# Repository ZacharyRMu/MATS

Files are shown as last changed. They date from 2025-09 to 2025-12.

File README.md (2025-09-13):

# Mobile Antenna Tracking System (MATS)

<p align="center">
  <picture>
    <source media="(prefers-color-scheme: dark)" srcset="docs/images/MATS_Logo_White.png">
    <source media="(prefers-color-scheme: light)" srcset="docs/images/MATS_Logo_Black.png">
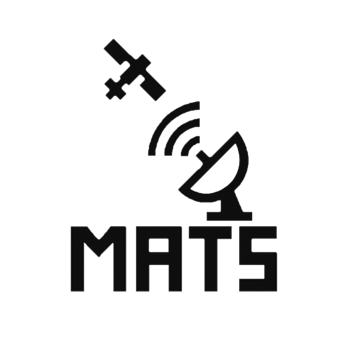
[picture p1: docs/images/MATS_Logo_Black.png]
MATS Logo
    
  </picture>
</p>

## Overview
MATS (Mobile Antenna Tracking System) is a portable ground station platform designed to automatically track and recieve data from Low Earth Orbit (LEO) weather satellites. The system integrates: 
- Reciever Subsystem - Raspberry Pi 5 with SDR Hardware, SatDump, SDR++, and GPS timing. 
- Rotator Subsystem - Motorized antenna rotator with gearing and fixture assembly for precise azimuth/elevation pointing. 
- User Interface (UI) - Touchscreen controls, pass scheduling via Gpredict, and system health/status indicators. 
- Power Subsystem - Regulated DC rails providing reliable power to the Pi, motors, and peripherals. 

## Features 
- Automated Satellite pass prediction and antenna tracking.
- Real-time SDR signal aquisition and decoding via SatDump.
- Portable Architecture for field deployments 
- Open, Modular Design for extensibility. 
## Installation and Setup 
1. Receiver Subsystem 
    - Flash Raspberry Pi OS on a Pi 5. 
    - Run the provided install script to set up SatDump, SDR++, Gpredict, and required libraries. 
    ```bash 
    cd Receiver
    ./batch_installer.sh
2. Rotator Subsystem
    - Assemble Mechanical fixture (CAD models in [placeholder]). 
    - Flash motor control firmware to microcontroller. 
3. UI Subsystem 
    - Connect Pi Touchscreen 
    - Run UI code to access controls and system status. 

## Usage
- Use **Gpredict** to select a satellite pass. 
- The **Rotator** will align the antenna in real time. 
- SatDump automatically records and decodes the downlink. 
- Results are stored in `/Receiver/Data/` and can be reviewed via the UI.

## License
This project is licensed under the GNU General Public License V3.0 (GPL-3.0). You may redistribute and modify it under the terms of the GPL as published by the Free Software Foundation. 

## Acknowledgements & External Software 
MATS leverages several excelled open-source projects: 
- [SatDump](https://github.com/SatDump/SatDump_) - Satellite signal demodulation and decoding. (Licensed under GPL-3.0)
- [SDR++](https://github.com/AlexandreRouma/SDRPlusPlus) - Software-defined radio receiver. (Licensed under GPL-3.0)
- [Gpredict](https://github.com/csete/gpredict) - Real-time satellite tracking and orbit protection. (Licensed under GPL-2.0)
- [VOLK](https://github.com/gnuradio/volk_) - Vector-optimized library of Kernels used by GNU Radio. (Licensed under GPL-3.0)

We extend sincere thanks to these communities for providing the tools that make this project possible.

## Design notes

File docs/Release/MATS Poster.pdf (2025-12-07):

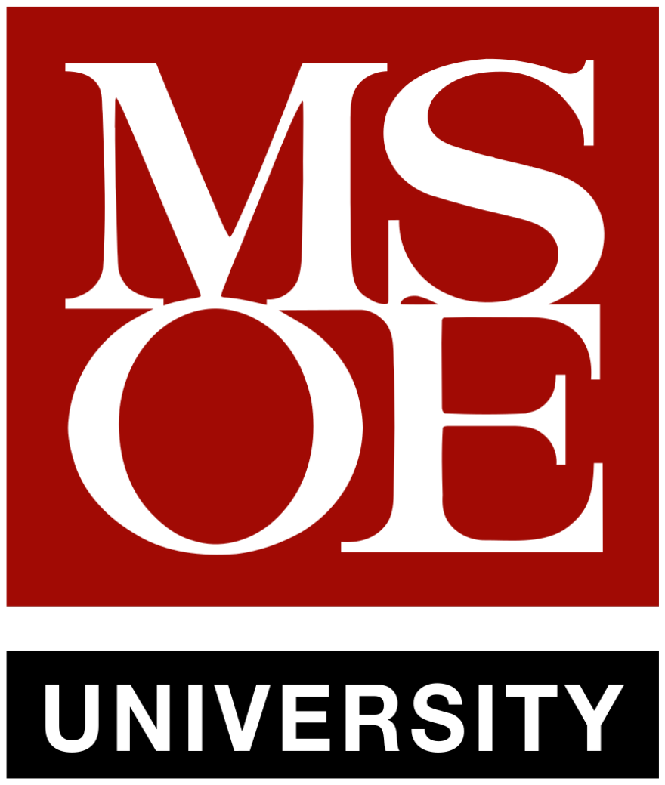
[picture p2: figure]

# MATS - Mobile Antenna Tracking System

# A Smart Portable Antenna Rotator and Satellite Receiver for Weather Imagery

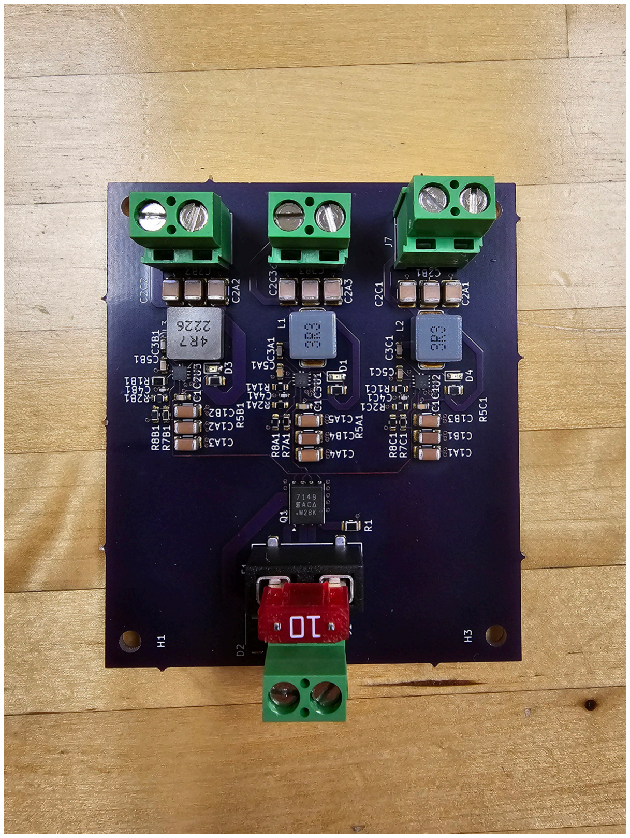
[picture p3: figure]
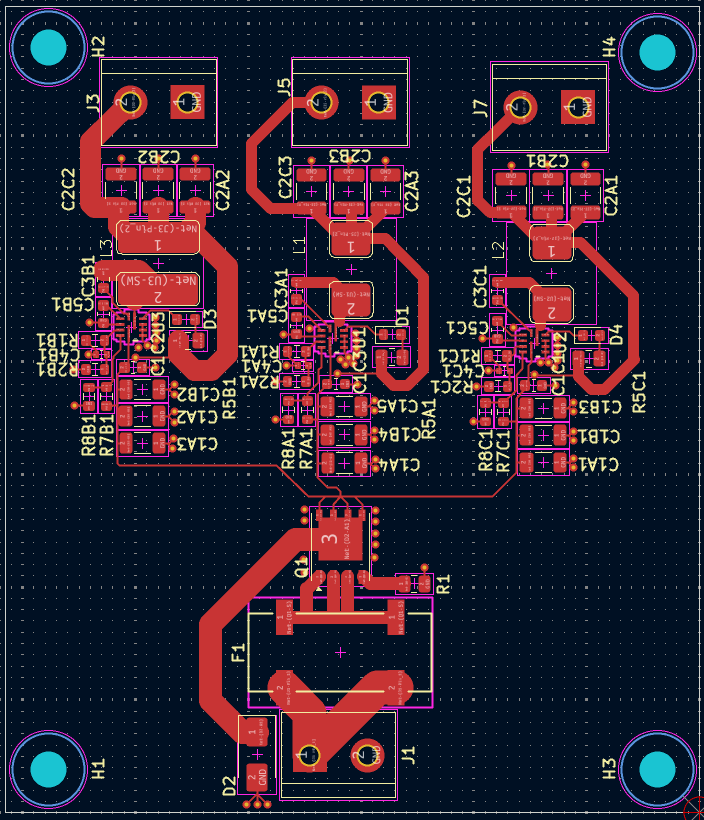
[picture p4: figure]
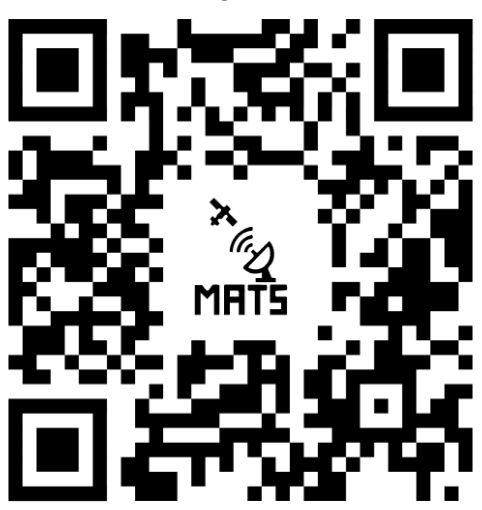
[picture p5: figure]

# Our Team

Zachary Murray, Dylan Vilcek, Ma Minghao

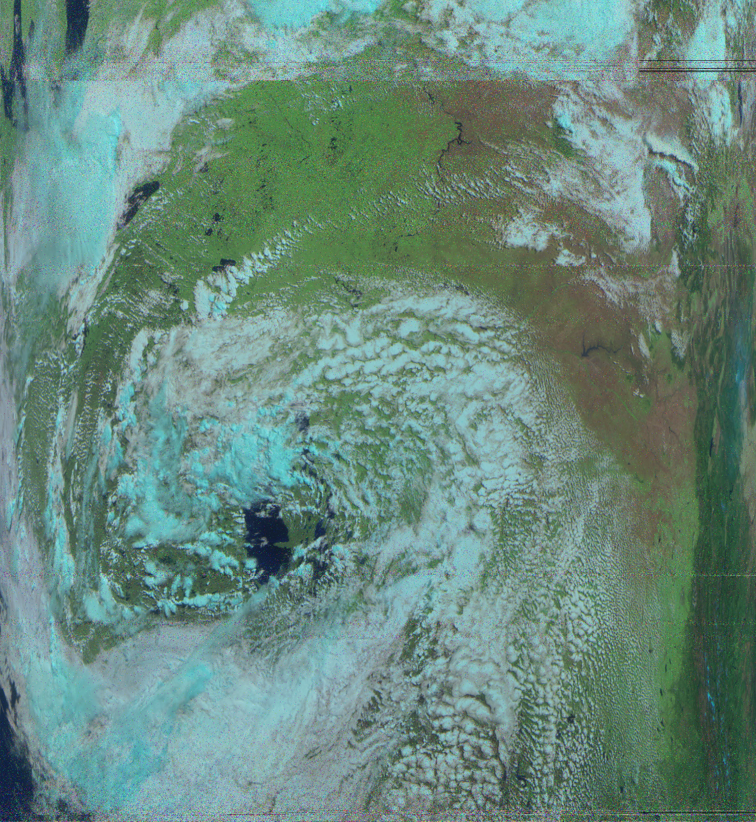
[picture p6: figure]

# Learn More

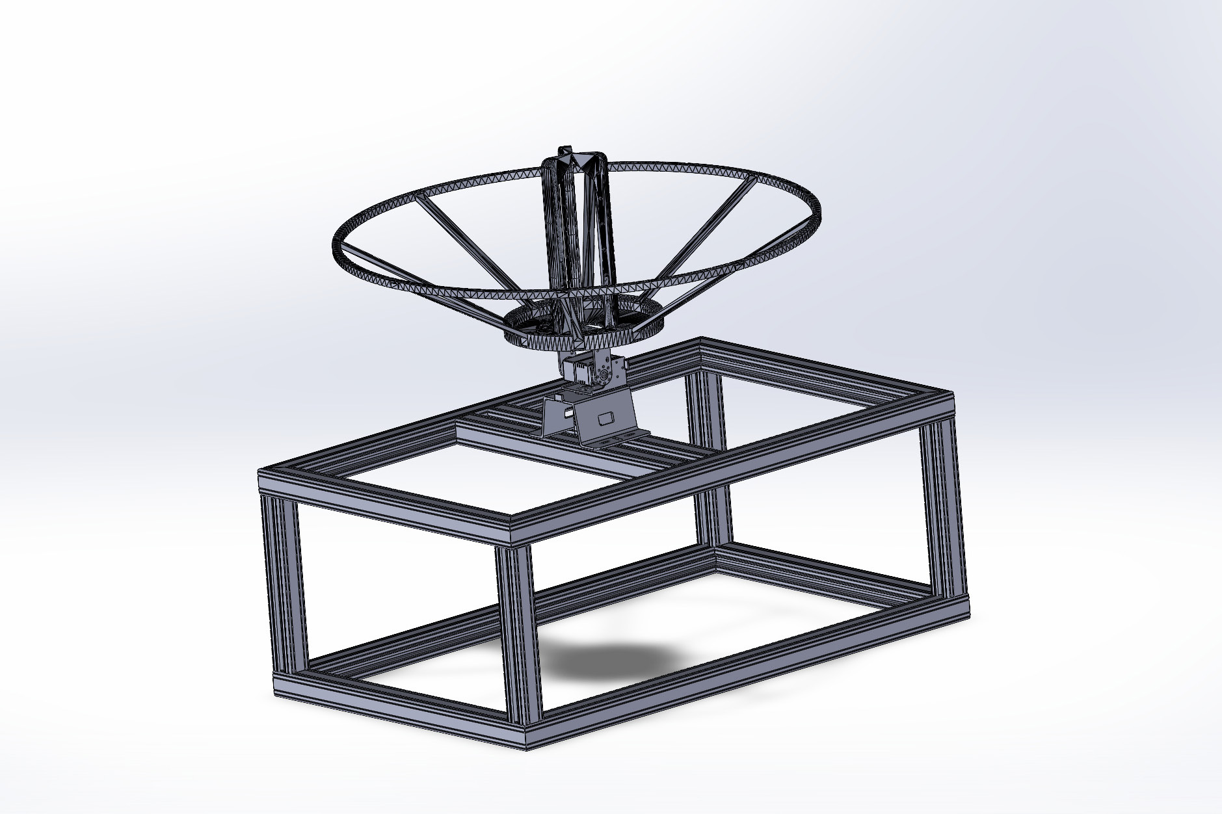
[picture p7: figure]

# System Block Diagram

The team would like to thank both Field Theory Consulting and MSOE alumnus Mr. Bob Radke for generous donations of materials for this project. Special thanks to our advisor, Dr. Kelnhofer for guidance and support.

# Acknowledgments

- Low cost, portable, and deployable on aircraft, ships, or field vehicles
- Operates from common on-board power (12-24VDC)
- Compact and Lightweight (<25 lbs, 22x14x9 in)
- Modular design supporting various types of antennas and receivers
- Reliably acquires and decodes L-band and other weather satellite signals
- Uses readily available hardware and open-source software

# Problem Statement

Existing satellite tracking systems are often expensive, proprietary, and difficult to use. MATS provides an open, modular platform for precise, automated multi-axis tracking and reception, designed for off-grid pilots, emergency crews, researchers, and educators.

# System Goals

# Technical Targets

- Achieve automated azimuth/elevation tracking within 1%
- Integrate GPredict tracking data over I²C
- Provide modular power rails (7.5 V, 5 V, 3.3 V)
- Support open-source SDR decoding (SatDump)

Power System PCB Layout and Assembly

Example Satellite Weather Imagery Captured

Pictured: Mechanical System

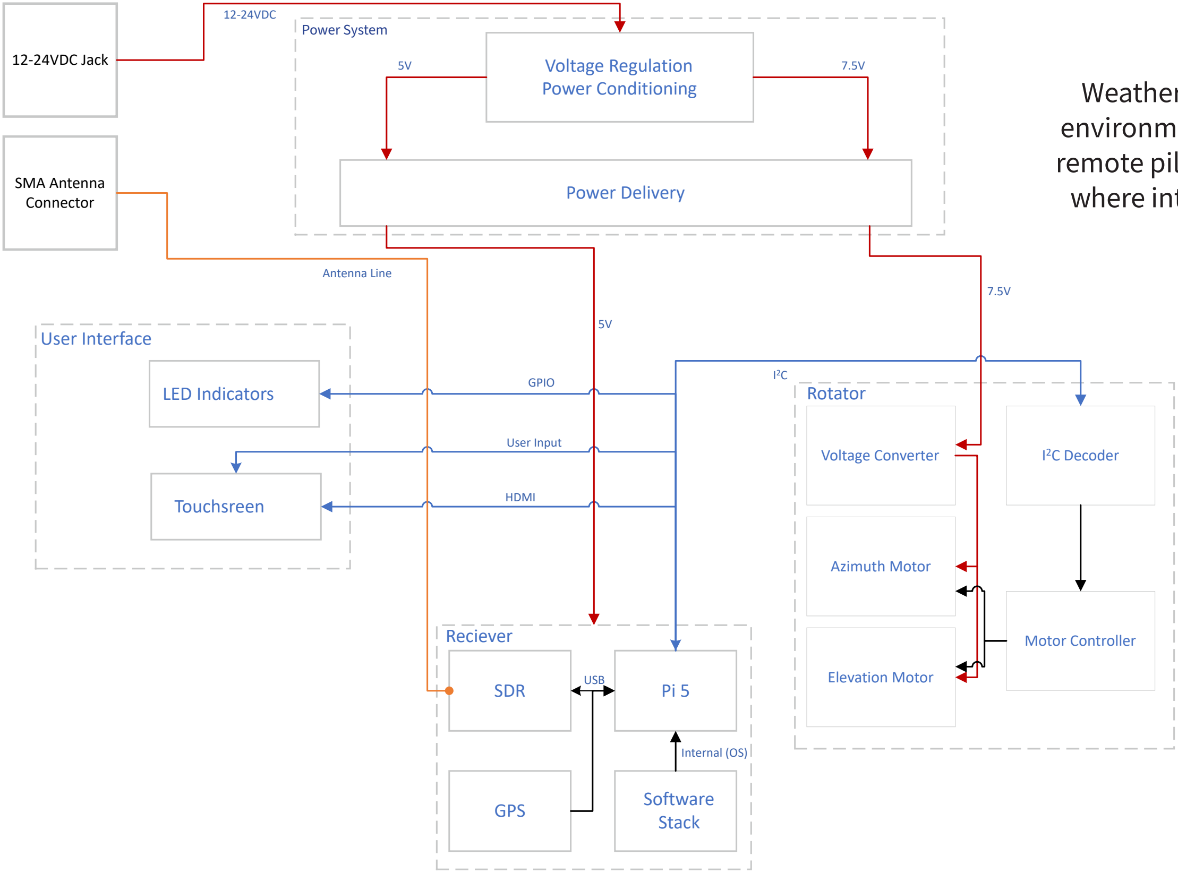
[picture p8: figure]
User Interface; Voltage Converter; Azimuth Motor; Elevation Motor; 2C Decoder; Reciever; Motor Controller; SDR; Software Stack; GPS; USB; Internal (OS); LED Indicators; Rotator; Touchsreen; HDMI; GPIO; User Input; Voltage Regulation Power Conditioning; Power Delivery; 12-24VDC Jack; SMA Antenna Connector; Antenna Line; 12-24VDC; Power System

Weather imagery provides critical near real time environmental data for emergency response crews, remote pilots, and research crews stationed in areas where internet may not be available or expensive.

## Find the Project on GitHub

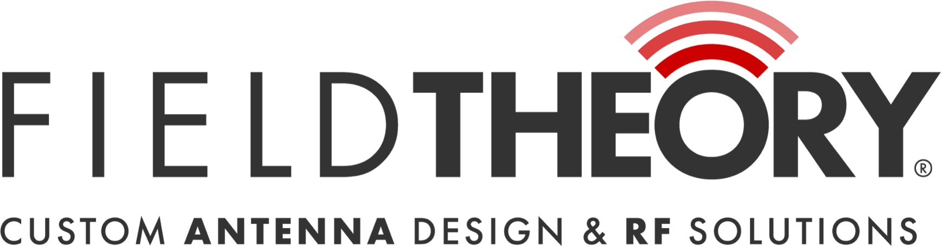
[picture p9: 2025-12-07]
docs/images/fieldtheory.jpg

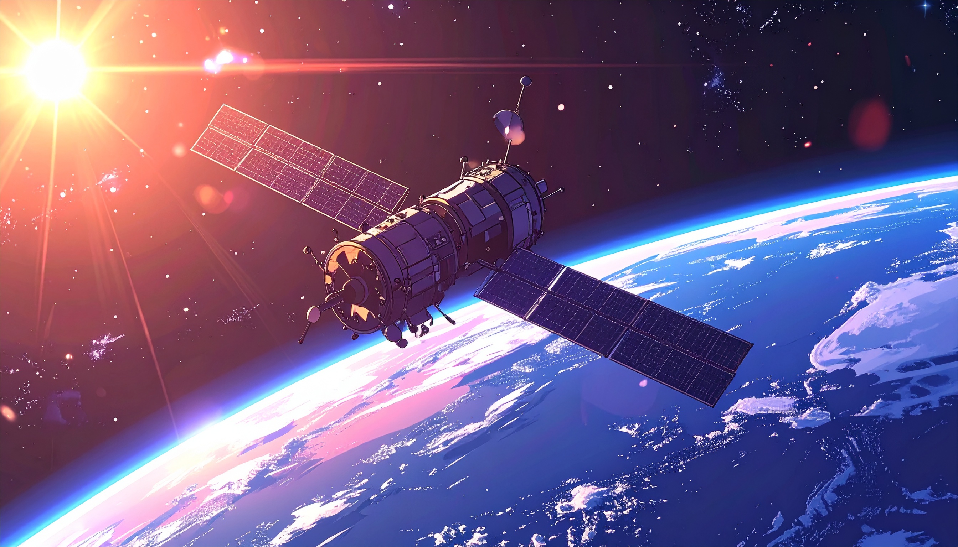
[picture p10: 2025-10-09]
docs/images/MATS_Background.jpg

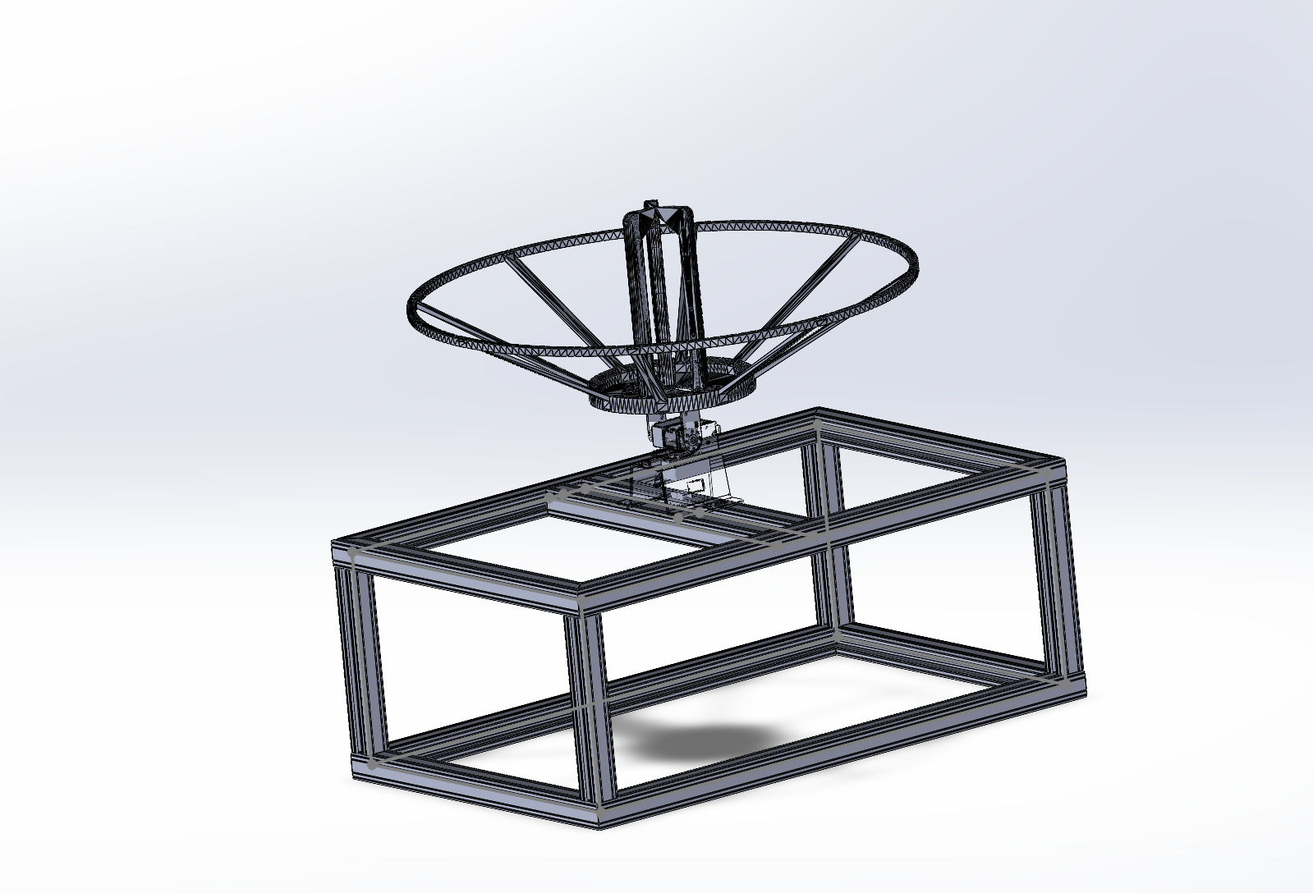
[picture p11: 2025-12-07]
docs/images/Screenshot 2025-12-01 123529.png

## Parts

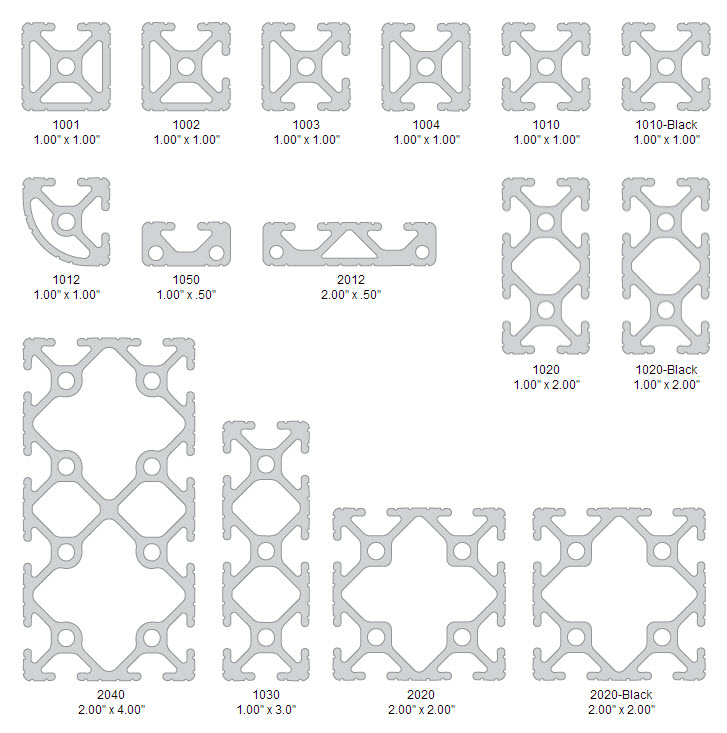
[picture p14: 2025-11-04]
Mechanicals/parts/weldment/Renderings/10_series_image_list.jpg

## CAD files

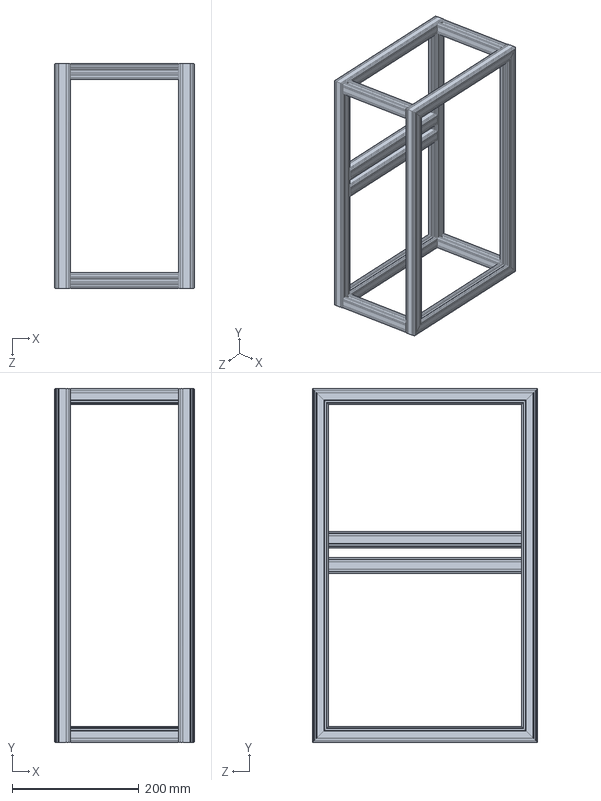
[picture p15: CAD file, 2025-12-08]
Mechanicals/Case/weldment.SLDPRT
221.5 x 558.8 x 355.6 mm

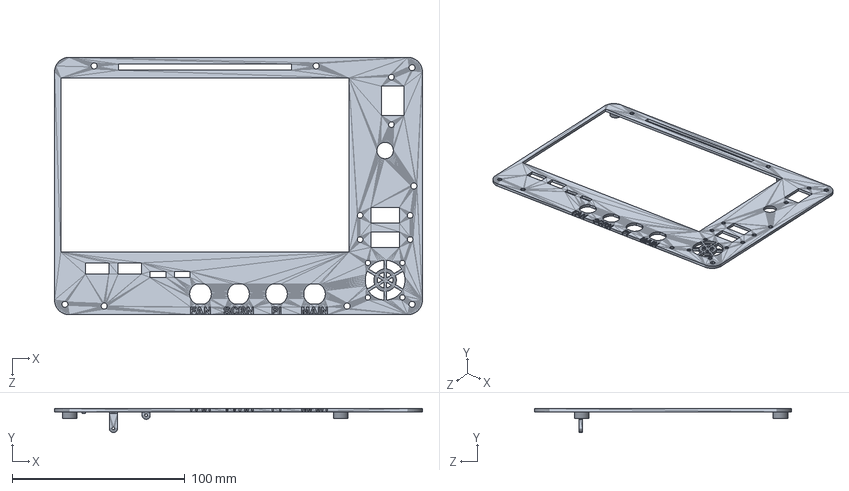
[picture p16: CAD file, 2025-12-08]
Mechanicals/parts/Screenpanel.SLDPRT
213.0 x 13.9 x 149.0 mm

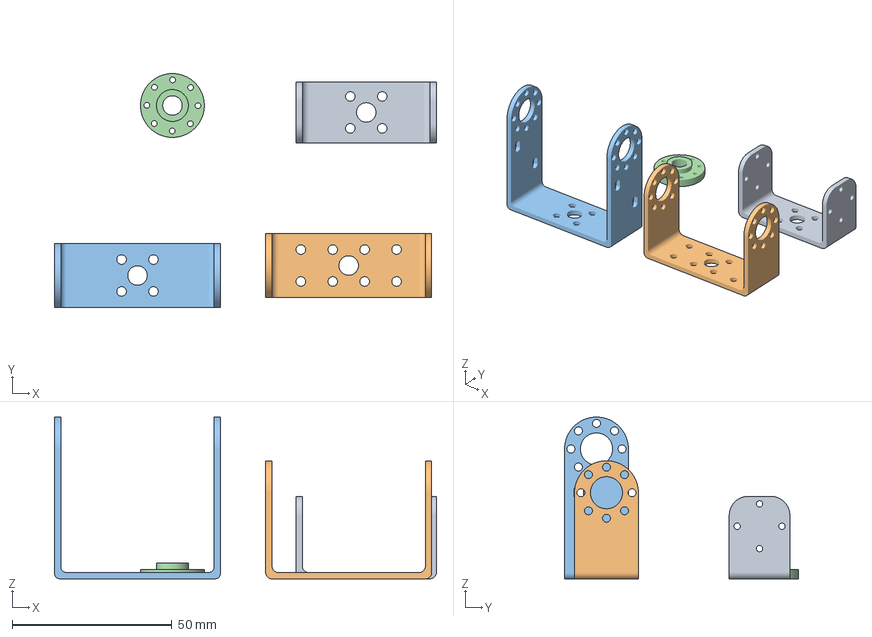
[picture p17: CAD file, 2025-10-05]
Mechanicals/Servo Motor Mount Print.3mf
119.6 x 73.2 x 50.7 mm
华馨京 25-50kg舵机系列U型舵盘支架（标准）-3D.STEP
华馨京 25-50kg舵机系列U型舵盘支架（37mm）-3D.STEP
华馨京 25-50kg舵机系列U型舵盘支架（50.7mm）-3D.STEP
华馨京 25-50kg舵机系列副舵盘-3D.STEP

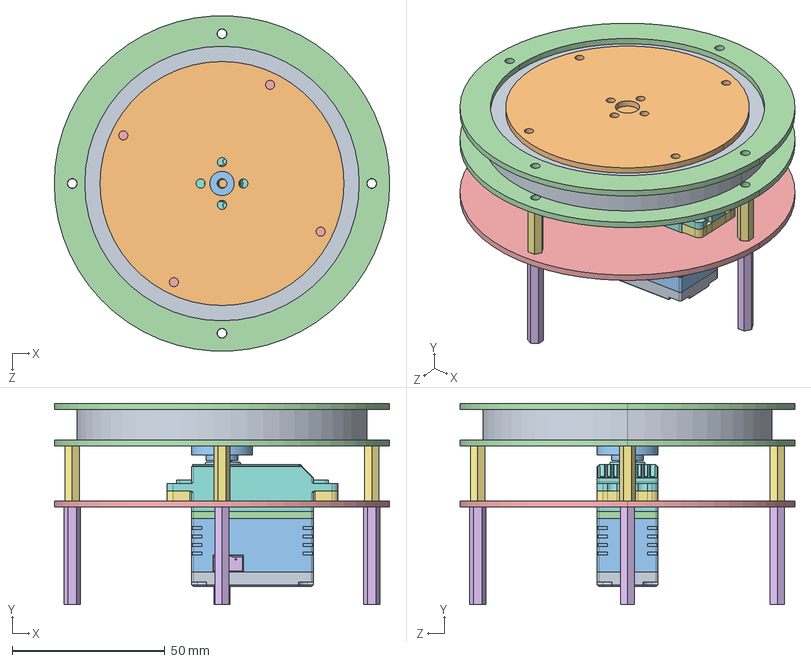
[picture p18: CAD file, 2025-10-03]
Mechanicals/华馨京科技 舵机云台系列图纸/华馨京科技 PD1-H-1 一维圆盘云台图纸/华馨京 圆盘云台-3D.STEP
110.0 x 66.0 x 109.8 mm
ZHOUCHENG^2自由度云台(2)_2自由度云台
ZHOUCHENGNEIBAN^2自由度云台(2)_2自由度云台 x 2
DUOPAN^2自由度云台(2)_2自由度云台
ZHOUCHENGWAIBAN^2自由度云台(2)_2自由度云台 x 2
ZHOUCHENGXIABAN^2自由度云台(2)_2自由度云台
TONGZHU32^2自由度云台(2)_2自由度云台 x 4
TONGZHU18^2自由度云台(2)_2自由度云台
TONGZHU^2自由度云台(2)_2自由度云台 x 4
____________.step.STEP
____________.step-0.STEP
______.step.STEP
____-____.STEP
________.STEP
3pin____.step.STEP x 2
单轴舵机垫片.stp x 2

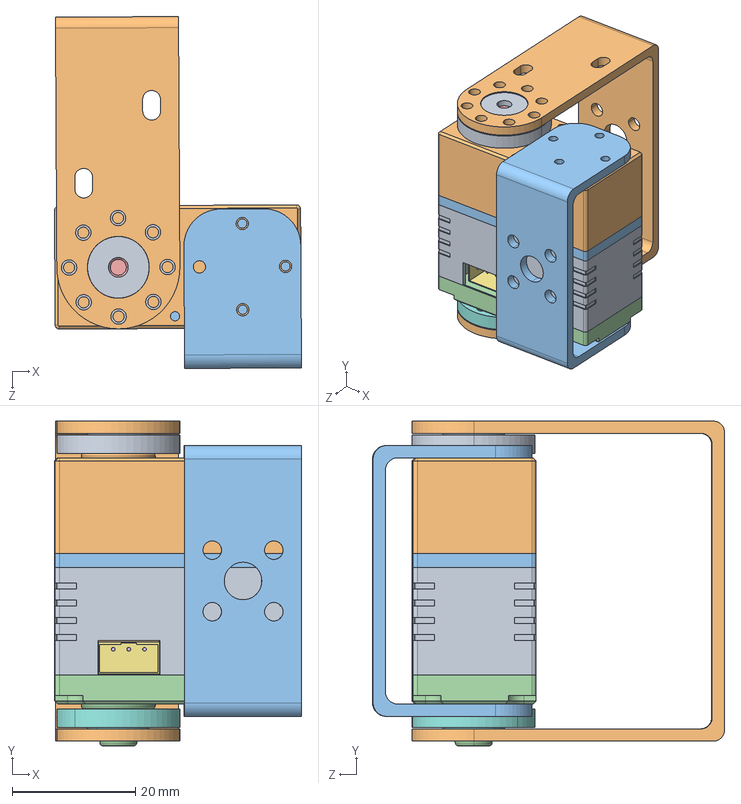
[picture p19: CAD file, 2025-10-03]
Mechanicals/华馨京科技 舵机云台系列图纸/华馨京科技 PD1-R-1 简易云台图纸/华馨京 简易云台-3D.STEP
40.1 x 52.8 x 57.2 mm
____-____.STEP
____________.STEP
________.STEP
____________-0.STEP
______.step.STEP
3pin____.step.STEP x 2
嗆攫ㄗ萵ㄘ
嗆攫ㄗ翋ㄘ
华馨京 25-50kg舵机系列长U1支架-3D
华馨京 25-50kg舵机系列小U支架-3D

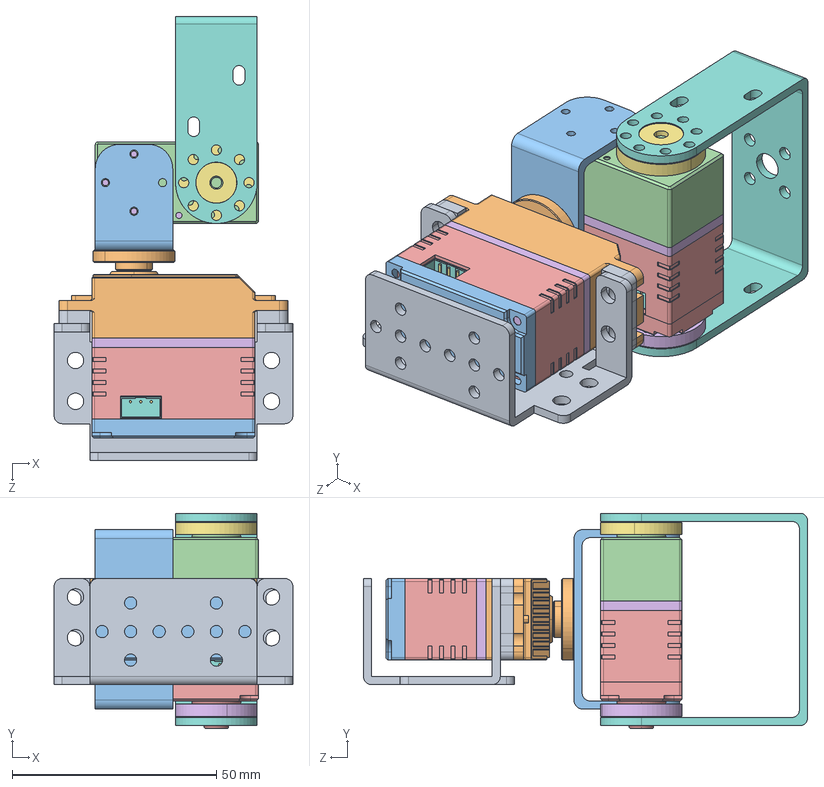
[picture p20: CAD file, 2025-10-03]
Mechanicals/华馨京科技 舵机云台系列图纸/华馨京科技 PD2-RH-1 二维多功能云台图纸/华馨京 多功能云台-3D.STEP
58.5 x 52.8 x 108.7 mm
多功能支架
____________.step.STEP
____________.step-0.STEP
______.step.STEP x 2
____-____.STEP x 2
________.STEP x 2
3pin____.step.STEP x 4
单轴舵机垫片.stp x 2
华馨京 25-50kg舵机系列主舵盘（四孔）-3D
华馨京 25-50kg舵机系列小U支架-3D
____________.STEP
____________-0.STEP
嗆攫ㄗ萵ㄘ
嗆攫ㄗ翋ㄘ
华馨京 25-50kg舵机系列长U1支架-3D

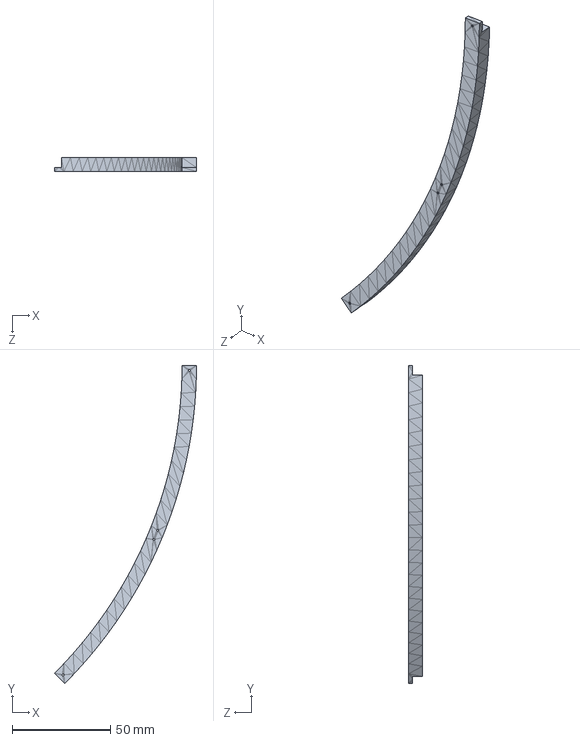
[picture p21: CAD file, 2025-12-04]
Mechanicals/parts/Upper_ring_x8.SLDPRT
72.4 x 162.1 x 7.00 mm

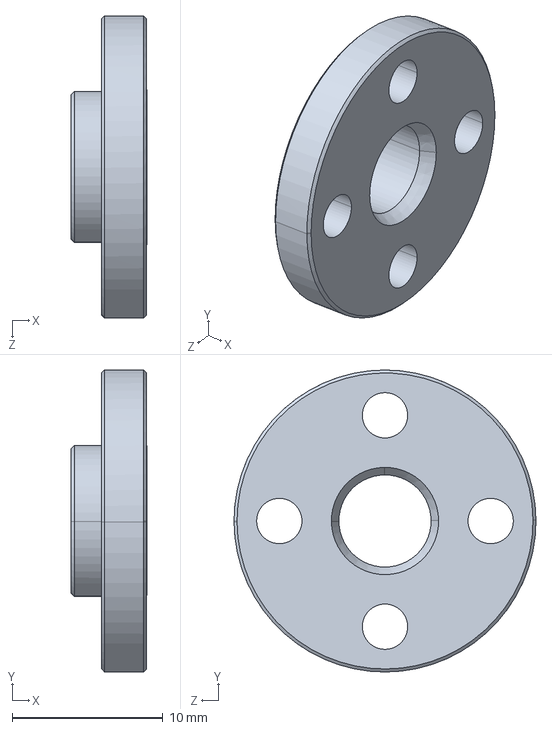
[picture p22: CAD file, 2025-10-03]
Mechanicals/华馨京 25-50kg舵机系列副舵盘（四孔）-3D.STEP
5.00 x 20.0 x 20.0 mm

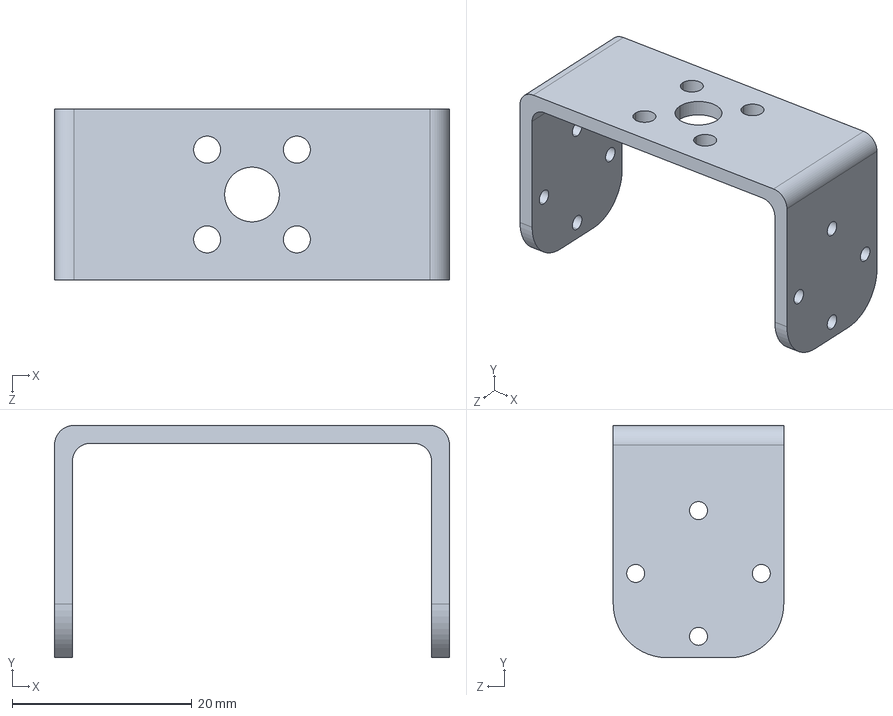
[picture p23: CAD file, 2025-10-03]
Mechanicals/华馨京 25-50kg舵机系列配件/华馨京 25-50kg舵机系列U型舵盘支架（标准）-3D.STEP
44.0 x 25.9 x 19.0 mm

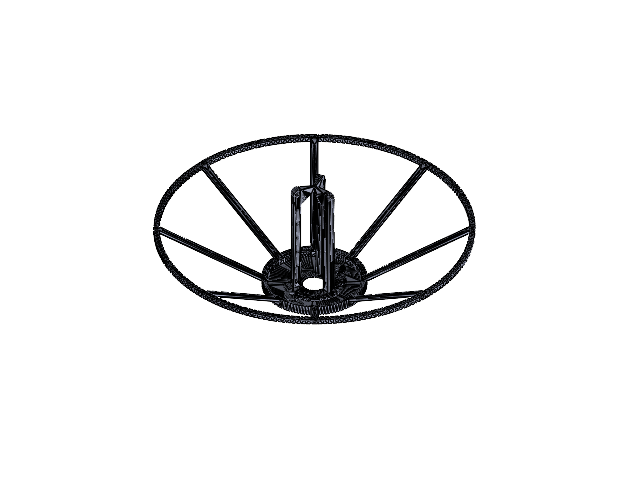
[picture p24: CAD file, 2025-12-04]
Mechanicals/parts/antenna.SLDASM
Base
Upper_ring_support_x8 x 8
Upper_ring_x8 x 8
helix_support_6.5T_1.7_Ghz

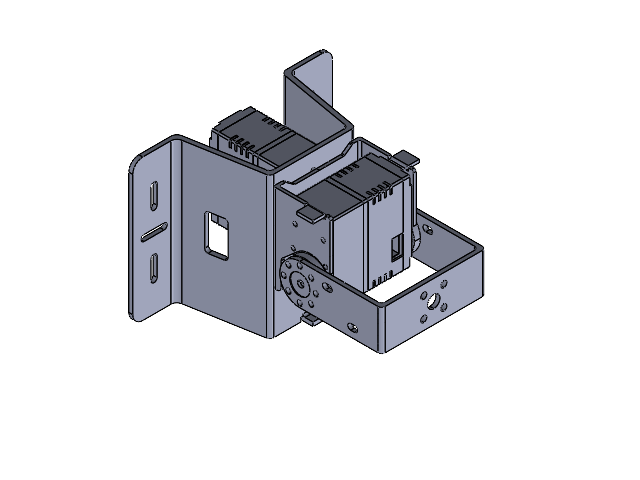
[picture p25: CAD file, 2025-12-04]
Mechanicals/parts/华馨京 OpenMV舵机云台-3D.SLDASM
____-____.STEP.STEP x 2
____________.STEP.STEP x 2
________.STEP.STEP x 2
____________-0.STEP.STEP x 2
______.step.STEP.STEP x 2
3pin____.step.STEP.STEP x 4
______________,______.STEP
__________.STEP
__________-0.STEP x 2
________________.step.STEP
__U________.STEP

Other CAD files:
Mechanicals/parts/weldment/001_t_slot_ty3_asm_27.sldasm
Mechanicals/parts/grainger-815GF4.sldasm
Mechanicals/parts/weldment/815gf5_2.sldprt
Mechanicals/华馨京 25-50kg舵机系列配件/华馨京 25-50kg舵机系列副舵盘尺寸图.dwg
Mechanicals/华馨京科技 OpenMV舵机云台图纸/华馨京 OpenMV舵机云台外观尺寸图.dwg
Mechanicals/华馨京科技 舵机云台系列图纸/华馨京科技 OpenMV舵机云台图纸/华馨京 OpenMV舵机云台外观尺寸图.dwg
Mechanicals/华馨京科技 舵机云台系列图纸/华馨京科技 PD2-RH-2 二维大支架云台图纸/华馨京 大支架云台外观尺寸图.dwg
Mechanicals/Case/Frame.SLDDRW
Mechanicals/parts/Base.SLDPRT
Mechanicals/parts/Base.stl
Mechanicals/parts/Dual-axis servo.SLDPRT
Mechanicals/parts/Dual-axis servo.STEP
Mechanicals/parts/Screenpanel.stl
Mechanicals/parts/Single axis servo.STEP
Mechanicals/parts/Upper_ring_support_x8.SLDPRT
Mechanicals/parts/Upper_ring_support_x8.stl
Mechanicals/parts/Upper_ring_x8.stl
Mechanicals/parts/antenna_mount.SLDPRT
Mechanicals/parts/helix_support_6.5T_1.7_Ghz.stl
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

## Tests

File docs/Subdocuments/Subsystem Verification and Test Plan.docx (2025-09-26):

MATS Subsystem Test Plans

Mobile Antenna Tracking System (MATS)

9/26/2025

Zachary Murray, Dylan Vilcek, Ma Minghao


This document outlines the subsystem verification and test plan for the MATS. This document will outline the objectives of testing each subsystem, equipment and software required, as well as the procedures to verify the proper operation of the individual subsystems for successful integration into the overall system.

Revision | Date | Author | Description
0.1 | 9/26/2025 | MATS Team | Initial draft created

# Receiver

## Subsystem Overview

The receiver is responsible for being the central processor for the MATS. Its duties include being able to track a satellite given the TLE’s in Gpredict, receiving signals from the tracked satellites and decode the signals using SatDump. The receiver is equipped with an RTL-SDR for signal reception and utilizes a Raspberry Pi 5 running Raspian OS for its wide software support and community. Additionally, the Receiver subsystem will be equipped with GPS such that SatDump can accurately decode the received signals with map overlays and timestamps. To support the tracking of the satellite, the Receiver utilizes its GPS coordinates and the TLE data given by Gpredict and sends position data to the Rotator.

## Subsystem Requirements and Specifications

To enable the Receiver to function accurately and be integrated into the MATS successfully, the Receiver has the following signal characteristics and requirements.

Table 1: Receiver Subsystem Requirements

Receiver Subsystem
Power Requirement | 5VDC 5A
I/O Characteristics | USB2-A Interface HDMI I2C
Receiving Equipment | 50Ω Antenna line External SMA Antenna Connector
Software | Raspbian OS SatDump Gpredict RTL-SDR drivers/software

## Objectives

The objectives for testing the receiver include verifying that the receiver has the correct drivers and software stack, being able to receive satellite communication downlinks, and decode these downlinks into meaningful data. Subsystem components that will be tested include:

- Installation of the correct RTL-SDR Drivers
- I2C enabled
- Correct software stack installed
  - SatDump
  - GPredict
  - GPS Driver
  - SDR++
- Reception of common satellites
- Satellite transmission decodes

These objectives ensure that the receiver can correctly send commands via I2C, receive and decode Satellite transmissions. Early testing to verify the I2C bus sends the correct 32 bits will also be executed, ensuring smooth integration with the rotator.

## Required Equipment

The required equipment to test the Receiver can be found below. Additionally, the testing scripts and programs can be found at the project’s GitHub[^1]. Required hardware testing is as follows:

- Receiver hardware
- Analog Discovery 2
- V-Dipole if testing VHF or equivalent L-band antenna if testing using L-band (can substitute for other antennas as region requires.)
- Multimeter

Optional equipment is listed below for use with certain testing scripts and hardware but not necessarily required:

- Laptop with serial port
- NanoVNA
- LNA/LNB for satellite reception (Satellite Dependent)

## Testing Procedure

### Correct Drivers Installed

Installation of the correct RTL-SDR drivers is crucial. The installer script should fetch the latest version, build, and install the correct driver. However, sometimes Udev rules can become a problem and not allow the correct RTL-SDR driver to initialize; it’s important that it is checked to verify that the correct driver is installed, and the generic driver be disabled. To ensure that the correct drivers are installed, Table 2 outlines the procedure to be followed.

Table 2: Correct RTL-SDR Driver Install Test Procedure

Test | Expected Result | Observed Result
Check that DVB and rtl12832 drivers are not loaded using lsmod | Drivers not loaded
Plug in RTL-SDR V4 into Receiver | N/A | N/A
Run lsusb to confirm the device is detected | RTL-SDR found
Run rtl_test -t or rtl_test -p to verify the driver claims the device | No "usb_open error" message

### I2C Interface Enablement

Verify that the Raspberry Pi’s I2C interface is enabled by the installer script and accessible by user-space applications. Table 3 outlines this procedure.

Table 3: I2C Interface Testing

Test | Expected Result | Observed Result
Inspect /boot/firmware/config.txt
Confirm dtparam=i2c_arm=on is present and not commented out | Line not commented out
Verify the invoking user has been added to the i2c group
run the following: groups $USER | grep i2c | User Added
Verify the kernel driver is loaded. Run: lsmod | grep i2c_bcm | Driver loaded
With the system booted, execute: sudo i2cdetect -y 1 | A grid of addresses is displayed
Use the Analog Discovery 2 to verify I2C traffic using the provided i2c_ad2_test.py script. | I2C present on AD2

### Installed Software Stack

The receiver must have the correct software stack for correct operation with the other subsystems. This test section ensures that the correct software, such as GPS drivers, SatDump, Gpredict, and SDR++ are installed on the system. Table 4 shows the procedure. A test script has been provided in the github repository for automated testing.

Table 4: Receiver Software Stack Test Procedure

Test | Expected Result | Observed Result
Run automated verification script | Script executes and prints results for each component.
Check GPS drivers | Output shows: [+] Checking gpsd... PASS
Check SatDump installation | Output shows: [+] Checking SatDump... PASS
Check Gpredict installation | Output shows: [+] Checking Gpredict... PASS
Check SDR++ installation | Output shows: [+] Checking SDR++... PASS
Review summary | Script ends with === Verification complete === and no FAIL messages.

### Satellite Reception

Successful satellite reception is required for the MATS to perform it’s core functionality. Shown below in Table 5, the testing procedure verifies that that SatDump can record a satellite transmission.

Table 5: Satellite Reception Test

Test | Expected Result | Observed Result
Connect RTL-SDR Blog V4 dongle to Pi USB 3.0 port and attach VHF antenna (QFH, V-dipole, turnstile, etc.) tuned for ~137 MHz. | Hardware connected firmly, antenna outdoors or with clear sky view.
Use Gpredict to check upcoming Meteor-M2-4 pass (137.9 MHz). Record start time, max elevation, and pass duration. | Pass info visible, frequency: 137.900 MHz.
Launch SDR++ and configure RTL-SDR input. Set center frequency to 137.9 MHz and sample rate to ~2.048 MSPS. | Device initializes without error, spectrum visible.
Observe waterfall during predicted pass. | Wideband (~140 kHz) signal appears centered at 137.9 MHz, rising above noise floor as pass begins.
(Optional) Verify via SatDump spectrum mode without decoding. | Console/log shows device streaming, RF power increases near 137.9 MHz during pass.
Monitor until end of pass. | Signal fades as satellite sets. No USB or driver errors reported.

### Satellite Transmission Decoding

Testing of the receiver’s decoding stack ensures that satellite transmissions are accurately reconstructed with the correct GPS coordinates and map overlays. Table 6 below outlines the testing procedure.

Table 6: Satellite Transmission Decode Test

Test | Expected Result | Observed Result
Connect RTL-SDR Blog V4 dongle to Pi USB 3.0 port and antenna suitable for target satellite (e.g., QFH for VHF). | Hardware connected firmly, antenna with clear sky view. | Hardware connected firmly, antenna with clear sky view.
Use Gpredict to schedule and monitor an upcoming pass of a decodable satellite (e.g., NOAA APT at 137.1–137.9 MHz or Meteor-M2-4 at 137.9 MHz). | Pass data visible with start time, elevation, and duration.
Launch SatDump in live mode with correct frequency and sample rate. | SatDump initializes without error, SDR engaged.
Observe console/log during pass. | Frames are received and decoded; progress messages visible.
At end of pass, review generated products (e.g., map overlays, imagery, data files). | Output files (e.g., PNG, HDF5) are generated in SatDump output directory with valid content.

## Subsystem Test Results

After execution of all test sections (drivers, I2C, software stack, reception, and decoding), results should be consolidated in the following table.

Test Section | Pass/Fail | Notes
RTL-SDR Driver Install
I²C Interface Enablement
Software Stack Verification
Satellite Reception (M2-4, 137.9 MHz)
Satellite Transmission Decoding

# User Interface

## Subsystem Overview

The User Interface subsystem provides the primary operator touchpoint within the MATS. It delivers feedback through a 7” touchscreen, communicates system status via LED indicators, and provides removable media access through USB and SD ports. The UI runs a lightweight Raspberry Pi OS desktop, auto-launching SatDump at startup. Status LED’s are driven using a Python daemon that subscribes to SatDump telemetry, providing live feedback for RF lock, recording, and power state.

## Subsystem Requirements and Specifications

Table 7: User Interface Subsystem Specifications

Category | Requirement
Display | 7 Inch capacitive touchscreen with Linux driver support.
Inputs/outputs | ≥1 USB-A user port, SD/microSD card reader, power switch, RF & Power status LEDs.
Environmental | Operating 0ºC-50ºC, front panel IP-54 splash resistance
Electrical | Single 5V DC rail, ≤ 2A steady-state draw
Software | I2C touch controller, GPIO LEDs
Mechanical | Front-panel mounting to aluminum chassis, maximum depth behind panel ≤45 mm

## Objectives

The testing objectives for the User Interface are:

- Verify touchscreen responsiveness and accuracy
- Confirm automatic startup and SatDump launch.
- Validate USB and SD card hot-plug enumeration
- Verify LED indicators function under scripted test
- Confirm LEDs respond correctly to SatDump Telemetry.

These objectives ensure the User Interface provides reliable control and feedback to operators.

## Required Equipment

- UI Hardware
- Test Media: 32 GB microSD card and 128 GB USB Flash drive
- Multimeter
- Python I2C test script (led_test.py

## Testing Procedure

Testing of the user interface is primarily focused on the core functionality with interacting with the MATS. Table 8 shows the tests to be performed for successful verification.

Table 8: User Interface Testing

Test | Method | Expected Result | Observed Result
Display Touch Response | Run 10-point accuracy grid or calibration app | Touch deviation < 2 mm
SatDump Auto-Launch | Boot system and observe startup | Pi logs into desktop and SatDump auto-launches within ~15 s
USB Enumeration | Hot-plug 128 GB USB drive | Drive mounts automatically in <3 s
SD Card Enumeration | Hot-plug 32 GB microSD card via panel reader | Card mounts automatically in <3 s
LED Functionality | Run led_test.py scripted I²C pattern test | Each LED (Power, RF, Recording) cycles correctly through colors
LED Telemetry Response | Start/stop SatDump recording session | RF/Recording LEDs toggle in real time with telemetry

## Subsystem Test Results

Test Section | Pass/Fail | Notes
Touchscreen Accuracy
Auto-Launch of SatDump
USB Enumeration
SD Card Enumeration
LED Functionality
LED Telemetry Response

# Rotator

## Subsystem Overview

The purpose of this subsystem verification plan is to establish a structured and repeatable process for verifying the performance, functionality, and compliance of the Rotator subsystem. This document provides a detailed framework for conducting verification activities, ensuring that all requirements are met before integration into the larger MATS. By following this plan, verification activities will be performed efficiently, ensuring the subsystem meets its design and functional requirements before proceeding to the next phase of system development.

## System Requirements and Specifications

The MATS aims to be small, lightweight, and cost effective, providing an encompassing solution compared to other commercial systems, which are large, heavy, and expensive. The MATS encompasses all the hardware required to accurately position the antenna, according to the TLE information for a given satellite. Utilizing GPS for positional data, the only input the user requires is to know which satellite is passing overhead. The MATS will be deployed by supplying power from any power system onboard many aircraft, marine vessels, emergency vehicles, and power systems commonly found in developing communities. Figure 1 shows the overall system diagram, showing how the subsystems interact with each other. The requirements enable the MATS to be low cost and reliable, while still having accurate satellite tracking.

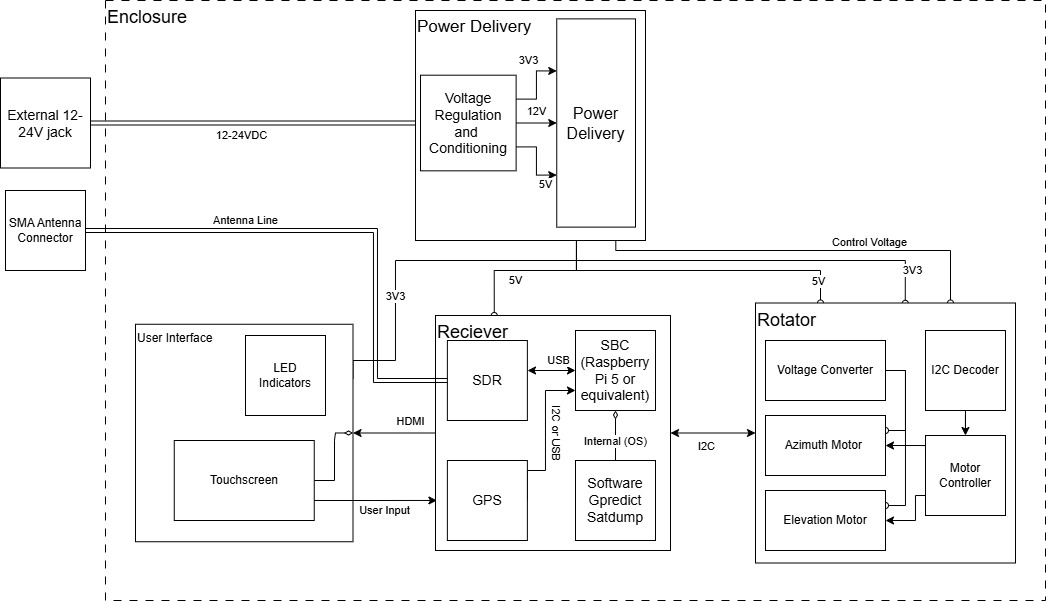
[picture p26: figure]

Figure 1: System Diagram

## Subsystem Requirements and Specifications

The Rotator system is responsible for rotating the antenna, moving it to a position given by the receiver system to track low earth orbit satellites. Due to the requirements given by the receiver, this system needs to receive an I2C signal for obtaining the azimuth and elevation location required and positioning the antenna to the specific coordinate within the specific time. System requirements can be found in Table 16.

Table 9: Rotator Subsystem Requirements

Requirement | Expectation
Power Requirement | 3V3, 12VDC
Interface | I²C
Azimuth Accuracy | ±1.6°
Elevation Accuracy | ±1.6°
Power Consumption | < 75W
Cost | < $110

A diagram is provided in Figure 2 outlining the functional blocks and connections within the Rotator.

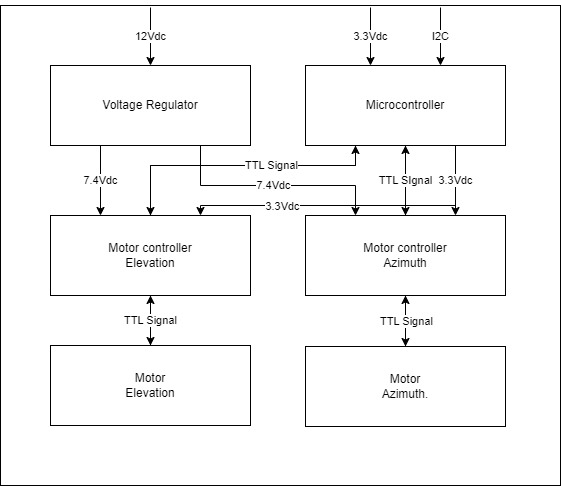
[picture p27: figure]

Figure 2: Rotator Block Diagram

These requirements ensure the proper operation of the Rotator, allowing the MATS to accurately track low earth orbit satellites.

## Objectives

These tests are intended to test the Rotator for proper operation. The rest of this document outlines the equipment and tests required to confirm that the Rotator is working as intended, and ready to be integrated into the larger MATS system. In these tests, the functional tests include:

- System Self-Test
- Azimuth Mobility Test
- Elevation Mobility Test
- Command Response Verification Test
- Rotational Mobility Test
- Power Consumption Test

## Required Equipment

For the following tests to be performed, some equipment should be obtained. This equipment is chosen for its simplicity of use and being readily available. The equipment required to perform these tests include:

- Laptop
- DMM
- Power Supply
- I²C Generator (raspberry pi, microcontroller, analog discovery)
- Stopwatch
- Protractor
- Wattmeter
- Compass

## Testing Procedure

This section details the verification procedures required to validate the Rotator. Each test ensures compliance with functional, performance, and reliability requirements. Data acquired from these tests should be documented in the provided tables.

### System Self-Test

The system self-test’s purpose is to verify that the azimuth and elevation motors start, perform the respective self-checks, and return to the original position. Table 10 outlines the procedure and measurements to be taken.

Table 10: System Self-Test Procedure

| Test/Verification Step | Expected Value | Measured Value | Pass or Fail
1 | Connect power supply to Subsystem Under Test (SUT) as shown in Figure 3. | N/A
2 | Using a protractor, take an initial position measurement at 90 degrees. | 90
3 | Turn on the power to the SUT and observe the behavior. | N/A
4 | Verify the servo motors have performed their self-start checks. | Servo 1 and 2 online
5 | Using the protractor, measure the position deviation from original position measured in step 2. | < 1.8°

If the Rotator’s motors successfully perform the startup self-checks and return to the original position, the Rotator should be tested for functional performance.

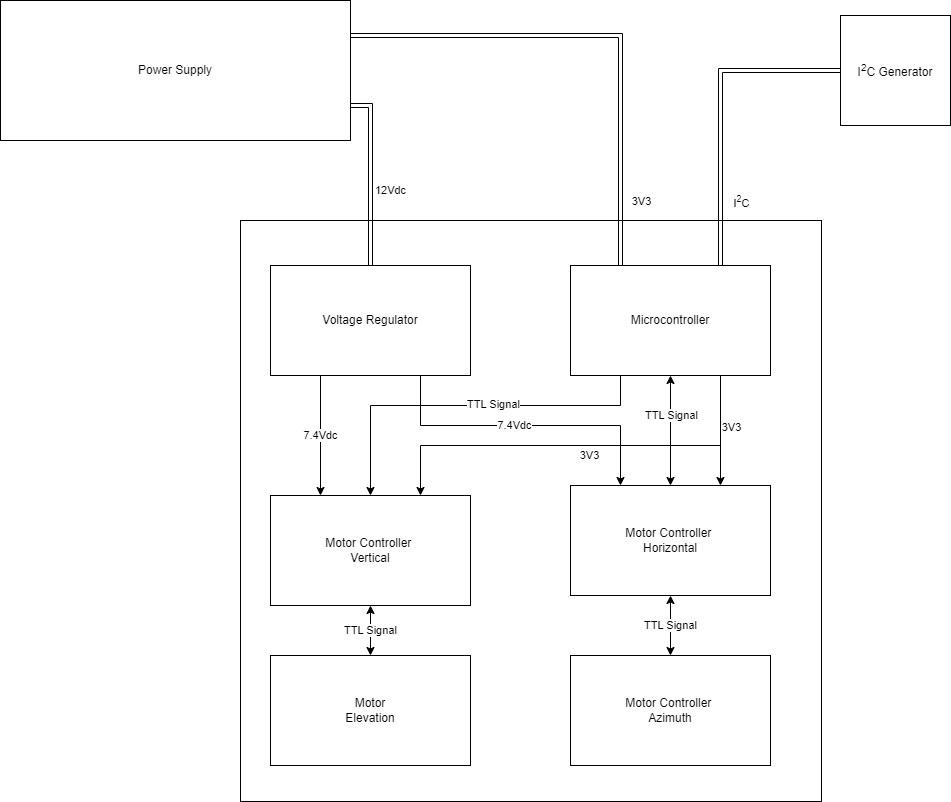
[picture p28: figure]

Figure 3: Mobility Test Setup

### Azimuth Mobility Test

The Azimuth Mobility Test verifies that the Rotator is capable of completely rotating 360 degrees in Azimuth. This check ensures that the Rotator will not need to “flip” when the satellite is passing directly overhead. This ensures that the signal will not be impacted while tracking directly overhead satellites.

To perform this test, the system should still be connected to power and the following steps outlined in Table 11 are to be performed.

Table 11: Azimuth Mobility Test Procedure

| Test/Verification Step | Expected Value | Measured Value | Pass or Fail
1 | Connect Test Equipment and power supply to Subsystem Under Test (SUT) as shown in Figure 3. | N/A
2 | Using a compass, take an initial measurement position measurement. | N/A
3 | Using the code provided in Figure 4, send a control input that moves the azimuth to rotate 90º. | N/A
4 | Utilizing the stopwatch, measure the amount of time taken to complete the rotation. | <180s
5 | Using the compass, measure the azimuth angle after rotation. | 90° ± 1.8°

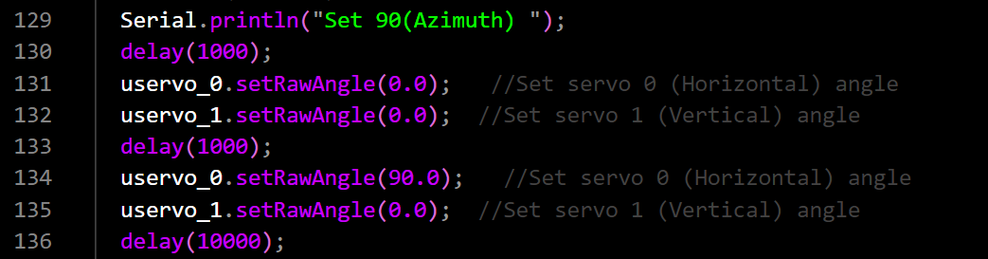
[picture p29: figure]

Figure 4: Azimuth Test Code

This check determines the freedom of movement of the Rotator subsystem’s azimuth direction. Upon failure, determine failure cause and document accordingly.

### Elevation Mobility Test

The Elevation Mobility Test determines the Rotator’s freedom in elevation. The elevation is where the antenna is pointed and is primarily responsible for holding the antenna at a given height above the horizon. This operation is required for proper signal strength, as deviations in elevation can lead to signal loss.

The procedure to outline this test is shown in Table 12.

Table 12: Elevation Mobility Test Procedures

| Test/Verification Step | Expected Value | Measured Value | Pass or Fail
1 | Connect Test Equipment and power supply to Subsystem Under Test (SUT) as shown in Figure 3. | N/A
2 | Using a compass, take an initial Elevation measurement. | N/A
3 | Using the code provided in Figure 5, send a control input that moves the elevation to 90º in elevation. | N/A
4 | Utilizing the stopwatch, measure the amount of time taken to complete the rotation. | <180s
5 | Using a compass, measure the elevation angle after the rotation is complete. | 90° ± 1.8°

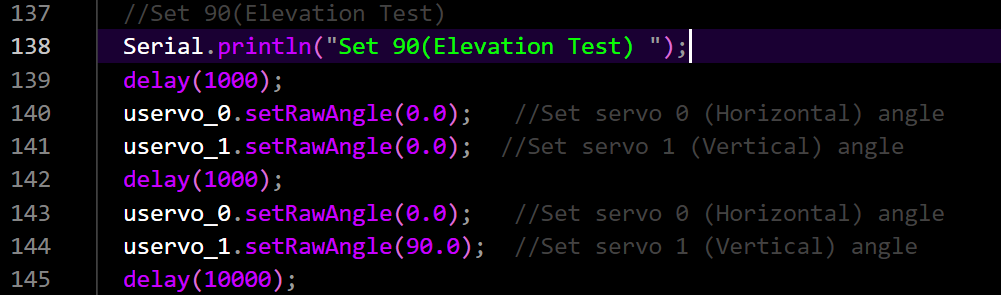
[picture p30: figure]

Figure 5: Elevation Test Code

Verification of this system ensures that the Rotator has freedom of movement in elevation, which enables smooth movement allowing for the least amount of signal loss. Upon failure, determine failure cause and document accordingly.

### Command Response Verification Test

The command response verification test ensures that the system can receive a command and move to the given coordinates. This test verifies that the Rotator can smoothly operate both the azimuth and elevation at the same time, ensuring that there is minimal signal loss during tracking.

To perform this test, follow the procedure outlined in Table 13.

Table 13: Command Response Verification Test

| Test/Verification Step | Expected Value | Measured Value | Pass or Fail
1 | Connect Test Equipment and power supply to Subsystem Under Test (SUT) as shown in Figure 3. | N/A
2 | Using a protractor, take an initial Elevation measurement at 0 degrees. | N/A
3 | Using the protractor, take an initial azimuth measurement at 90 degrees. | N/A
4 | Using the code provided in Figure 6, send a control input that moves 72º azimuth and 36º in elevation. | N/A
5 | Utilizing the stopwatch, measure the amount of time taken to complete the movement | <180s
6 | Using a compass, measure the elevation angle after the rotation is complete. | 36 ± 1.8°
7 | Using a compass, measure the azimuth angle after the rotation is complete. | 72 ± 1.8°

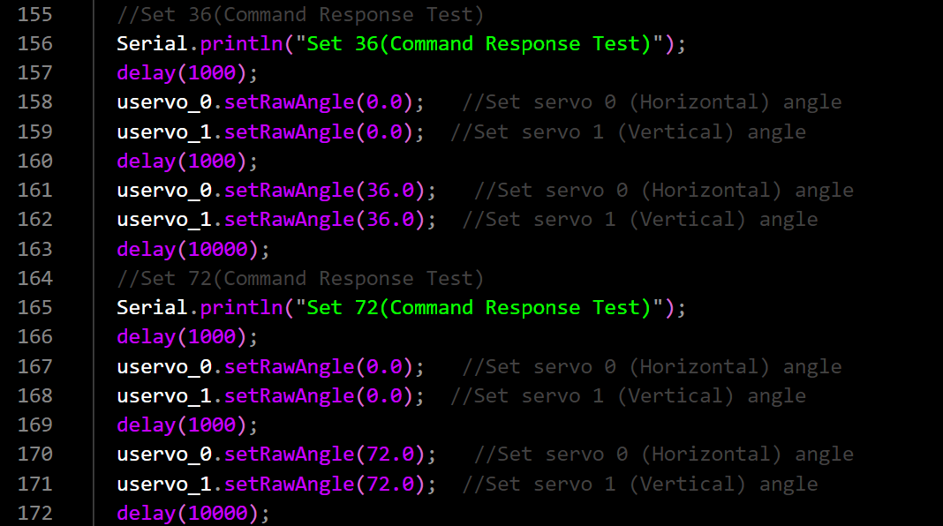
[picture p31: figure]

Figure 6: Command Response Test Code

Completion of this test ensures that the Rotator is capable of smoothly tracking and positioning an antenna where it needs to be for obtaining a good signal. Upon failure, determine cause and document accordingly.

### Rotational Mobility Test

The rotational mobility test will determine if the Rotator is capable of operating to the limit of azimuth and elevation required for accurate satellite tracking. This test will verify that the Rotator can move to more extreme values of azimuth and elevation.

To perform this test, follow the steps outlined in Table 14.

Table 14: Rotational Mobility Test

| Test/Verification Step | Expected Value | Measured Value | Pass or Fail
1 | Connect Test Equipment and power supply to Subsystem Under Test (SUT) as shown in Figure 3. | N/A
2 | Using a compass, take an initial Elevation measurement. | N/A
3 | Using the compass, take an initial azimuth measurement. | N/A
4 | Using code provided in Figure 8 And use Python code provided by Figure 9. send a control input that moves 172° azimuth and 86° in elevation. | N/A
5 | Utilizing the stopwatch, measure the amount of time taken to complete the movement | <180s
6 | Using a compass, measure the elevation angle after the rotation is complete. | 86 ± 1.8°
7 | Using a compass, measure the azimuth angle after the rotation is complete. | 172 ± 1.8°

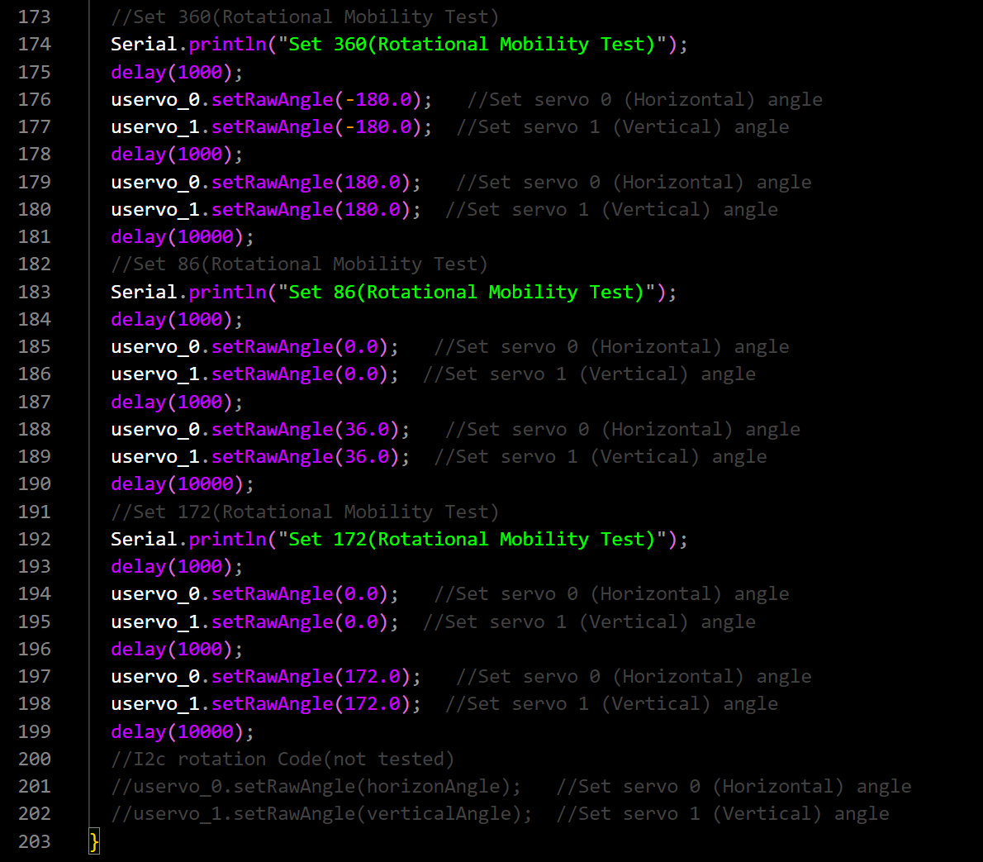
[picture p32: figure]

Figure 7: Rotational Mobility Test

Completion of this test ensures that the Rotator is capable of operating at the limits of required angles for tracking low earth orbit satellites. Upon failure, determine cause and document accordingly.

### Rotational Mobility Test by I2C

The rotational mobility test will determine if the Rotator is capable of operating to the limit of azimuth and elevation required for accurate satellite tracking by receiving system. This test will verify that the Rotator can receive correct messages from receive system and keep tracking right position.

To perform this test, follow the steps outlined in Table 14.

Table 7: Rotational Mobility Test

| Test/Verification Step | Expected Value | Measured Value | Pass or Fail
1 | Connect Test Equipment and power supply to Subsystem Under Test (SUT) as shown in Figure 3. | N/A
2 | Using a compass, take an initial Elevation measurement. | N/A
3 | Using the compass, take an initial azimuth measurement. | N/A
4 | Using code provided in Figure 7, send a control input that moves 172° azimuth and 86° in elevation. | N/A
5 | Utilizing the stopwatch, measure the amount of time taken to complete the movement | <180s
6 | Using a compass, measure the elevation angle after the rotation is complete. | 86 ± 1.8°
7 | Using a compass, measure the azimuth angle after the rotation is complete. | 172 ± 1.8°

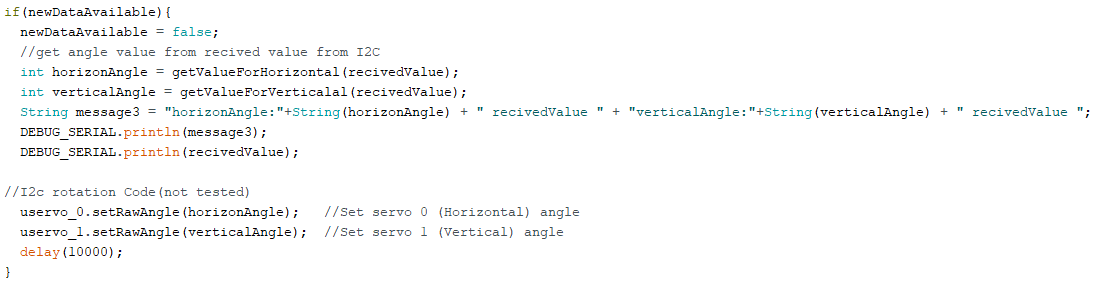
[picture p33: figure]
A computer screen shot of a code

Figure 8: Rotational Mobility Test

Completion of this test ensures that the Rotator can receive satellites location from reciver for tracking low earth orbit satellites. Upon failure, determine cause and document accordingly.

### Power Consumption Test

The power consumption test verifies that the MATS has a power consumption that enables it to perform utilizing available power on board many aircraft, emergency vehicles, and maritime vessels. Table 15 outlines the procedure to successfully perform these checks, and Figure 8 shows the set equipment setup.

Table 15: Power Consumption Test Procedure

| Test/Verification Step | Expected Value | Measured Value | Pass or Fail
1 | Connect Test equipment and the subsystem under test (SUT) as shown in Figure 8. | N/A
2 | Connect Power Supply to SUT. | N/A
3 | Using I²C, send a control input that moves 90º azimuth and 45º in elevation. | N/A
4 | Record power consumed by the SUT as measured by a wattmeter | < 50W

The power consumption test validates that the rotator operates with a power consumption that will not damage fuses, wiring and other equipment on board airplanes, emergency vehicles and maritime vessels.

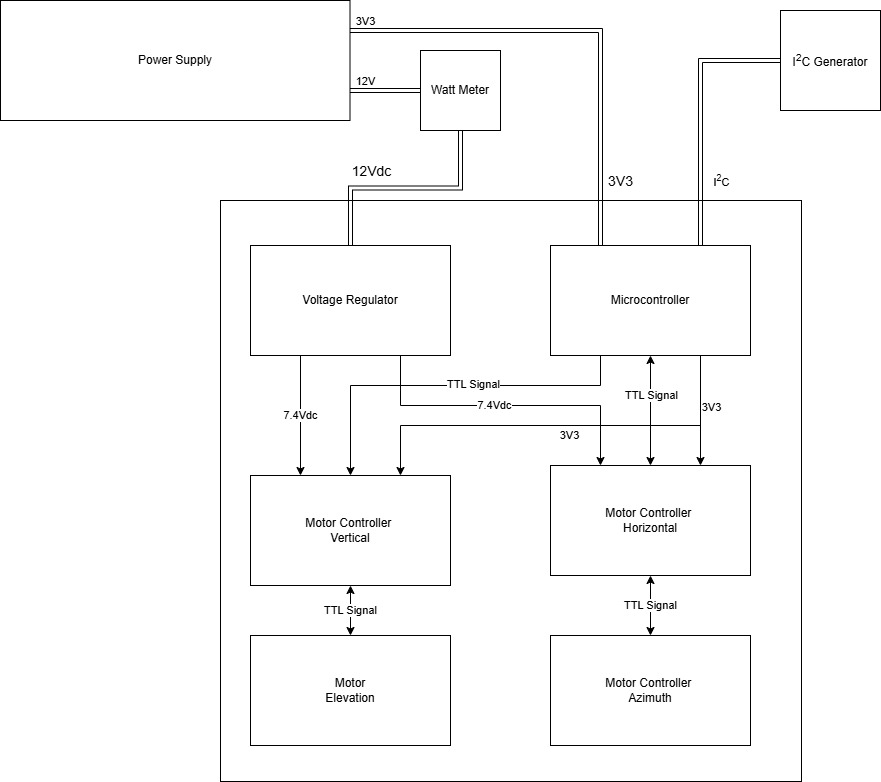
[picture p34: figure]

Figure 8: Power Consumption Equipment Setup
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

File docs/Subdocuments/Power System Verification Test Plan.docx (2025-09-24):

## Introduction

System overview and verification are critical to ensure that the MATS performs as intended. This document outlines the testing procedures for the Power Subsystem, which is responsible for converting the system’s 12–24 V input into regulated voltage rails required by all other subsystems. The Power Subsystem provides 7.5 V, 5 V, and 3.3 V outputs to support the Rotator, Receiver, and User Interface subsystems. This test plan aims to verify the proper functionality and reliability of the Power Subsystem independently, prior to integration into the full MATS system.

## Subsystem Requirements and Specifications

Using MP2329C buck converters, the design generates 7.5 V, 5 V, and 3.3 V outputs to supply the Rotator, Central Receiver, and User Interface. To ensure reliable operation, the subsystem must meet requirements for voltage accuracy, current delivery, ripple and noise, efficiency, and fault protection. System requirements can be found in Table 1.

Table 1: Rotator Subsystem Requirements

Requirement | Expectation
Input Voltage Range | 12-24 VDC
Output Rails | 7.5V, 5V, 3v3
Maximum Current | 6A, 5A, 5A
Voltage Accuracy | ± 5% of nominal
Ripple Voltage | ≤ 50 mVpp
Protection | Overcurrent and short-circuit safe

## Objectives

The objectives to test and verify operation for include:

1. Verify each output rail maintains voltage within tolerance across the load
2. Confirm maximum current delivery for each rail
3. Measure and evaluate ripple/noise
4. Validate startup, shutdown, and sequencing behavior
5. Test protection circuitry to ensure safe fault handling

## Required Equipment

The following is a list of the equipment needed to carry out the tests and verification plans for the Power Subsystem of the MATS.

- Programmable DC power supply
- Adjustable resistive loads
- Digital multimeter
- Oscilloscope

## Testing Procedure

This section covers in detail the testing procedure for each part of the Power Subsystem.

## Input Verification

Setup: Connect a programmable DC power supply to the subsystem input. Use a DMM to measure applied voltage and input current.

Procedure:

1. Start at 12 V input and increment in 2 V steps up to 24 V.
2. At each step, record input voltage and current draw with no load and with a representative load on each rail.

Acceptance Criteria: The subsystem powers on without fault at every step, and outputs remain stable within tolerance.

## Voltage Accuracy

Setup: Connect DMM probes to each output rail (7.5 V, 5 V, 3.3 V).

Procedure:

1. Apply nominal input voltage (e.g., 12V – 24V)
2. With no load, record output voltages.
3. Apply the rated load on each rail and record voltages of each rail.

Acceptance Citeria: Output voltages remain within ±5% (or tighter spec) of nominal.

## Load Regulation and Current Capacity

Setup: Connect adjustable resistive loads to each output rail.

Procedure:

1. Gradually increase load current on one rail up to its rated limit while monitoring voltage
2. Repeat for each rail independently, then with all rails loaded simultaneously.

Acceptance Criteria: Voltage deviation stays within limits, and subsystem does not shut down or overheat at rated load.

## Ripple and Noise

Setup: Connect an oscilloscope across each rail.

Procedure:

1. Apply nominal input voltage.
2. Record peak-to-peak ripple voltage for each rail.

Acceptance Criteria: Ripple and noise do not exceed spec (e.g., ≤ 50 mVpp or ≤ 100 mVpp for higher rails).

## Protection Testing

Setup: Use electronic loads for controlled overcurrent, and jumper wires for safe short-circuit testing.

Procedure:

1. Slowly increase load current beyond rated limit and observe whether the subsystem limits/shuts down safely.
2. Short each rail briefly (using current-limited setup) and confirm recovery behavior.

Acceptance Criteria: Protections engage without damage; system recovers after fault is removed.

## Conclusion

This test and verification plan defines the steps required to validate the MATS Power Subsystem against its design specifications. Successful completion will demonstrate that the subsystem can reliably provide regulated 7.5 V, 5 V, and 3.3 V rails from a wide input range, supply continuous load currents, maintain acceptable ripple, and withstand fault conditions without damage. The results will ensure the Power Subsystem meets the operational needs of MATS and provides a robust foundation for system integration.

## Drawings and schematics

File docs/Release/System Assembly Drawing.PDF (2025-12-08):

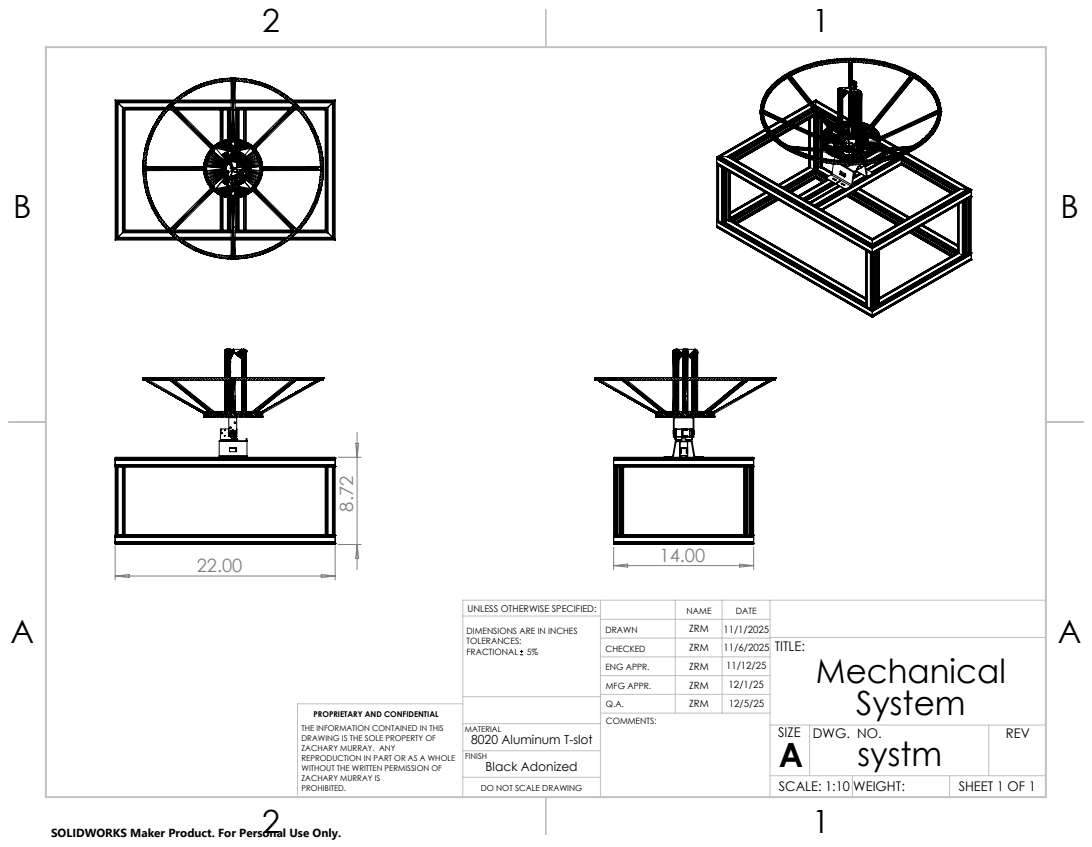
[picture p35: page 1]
SHEET 1 OF 1; SCALE: 1:10 WEIGHT:; DWG. NO.; REV

UNLESS OTHERWISE SPECIFIED: | | NAME | DATE
DIMENSIONS ARE IN INCHES TOLERANCES: FRACTIONAL 5% | DRAWN | ZRM | 11/1/2025

CHECKED | ZRM | 11/6/2025 | TITLE: Mechanical System
ENG APPR. | ZRM | 11/12/25
MFG APPR. | ZRM | 12/1/25
Q.A. | ZRM | 12/5/25

PROPRIETARY AND CONFIDENTIAL
THE INFORMATION CONTAINED IN THIS
DRAWING IS THE SOLE PROPERTY OF
ZACHARY MURRAY. ANY
REPRODUCTION IN PART OR AS A WHOLE
WITHOUT THE WRITTEN PERMISSION OF
ZACHARY MURRAY IS
PROHIBITED.

MATERIAL
8020 Aluminum T-slot
Black Adonized FINISH

DO NOT SCALE DRAWING

SOLIDWORKS Maker Product. For Personal Use Only.

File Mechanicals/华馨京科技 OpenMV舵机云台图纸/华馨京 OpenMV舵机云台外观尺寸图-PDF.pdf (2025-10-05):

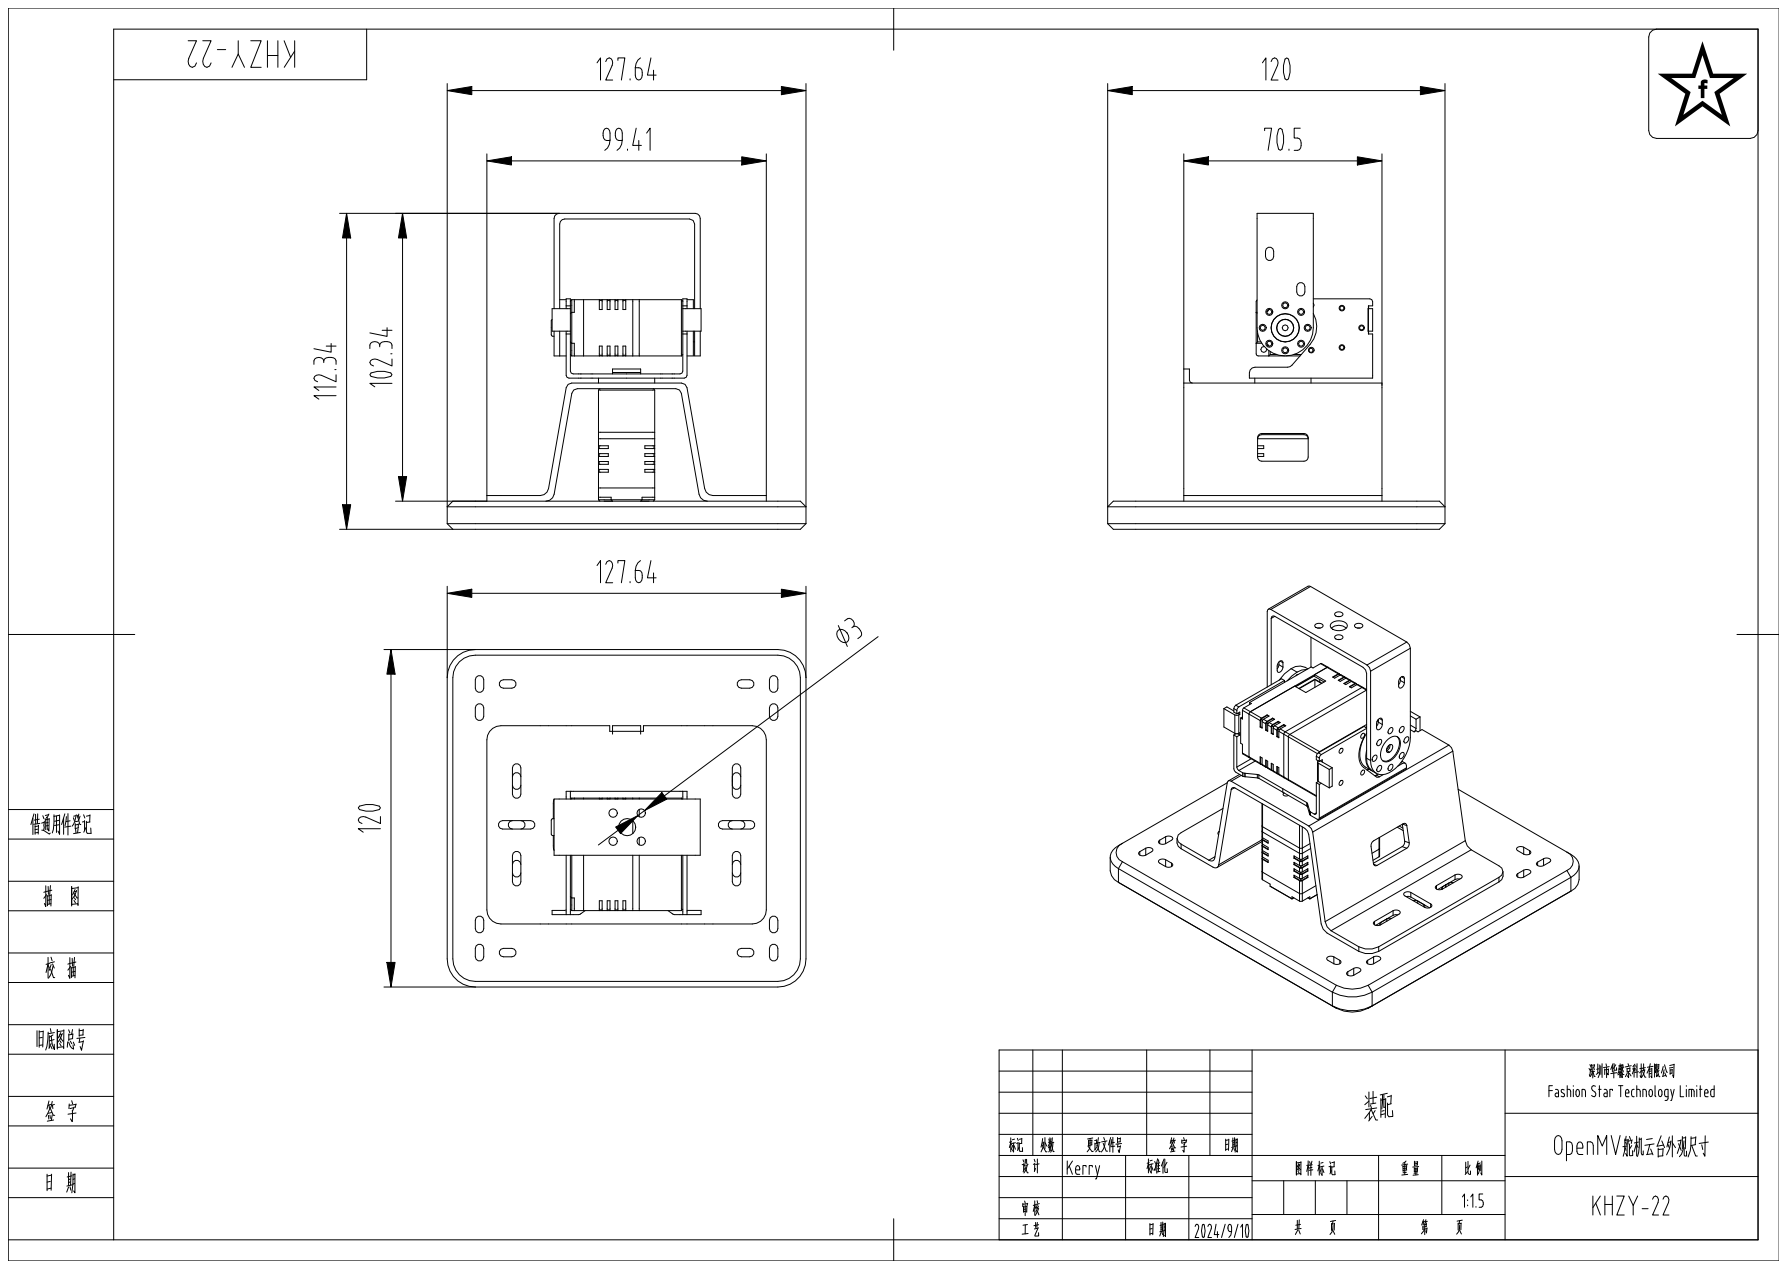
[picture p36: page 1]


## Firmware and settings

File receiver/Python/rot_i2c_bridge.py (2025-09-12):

#!/usr/bin/env python3
# file: rot_i2c_bridge.py
import asyncio, math, time
from typing import Tuple

# --- I2C hardware layer (PCA9685 example) -----------------------
USE_PCA9685 = True
if USE_PCA9685:
    from adafruit_pca9685 import PCA9685
    import board, busio
    i2c = busio.I2C(board.SCL, board.SDA)
    pca = PCA9685(i2c)
    pca.frequency = 50  # typical for hobby servos

# Servo config (adjust to your mechanics)
AZ_CH = 0
EL_CH = 1
AZ_MIN_DEG, AZ_MAX_DEG = 0.0, 360.0   # wrap allowed; we’ll clamp output mapping to your mechanics
EL_MIN_DEG, EL_MAX_DEG = 0.0, 90.0

# If your servo is only 0–180, set these to your usable range and mechanically gear for 360 azimuth.
SERVO_MIN_US = 500     # microseconds pulse ~0°
SERVO_MAX_US = 2500    # microseconds pulse ~180°
SERVO_RANGE_DEG = 180  # typical hobby servo travel

def us_to_12bit_duty(us: float, freq=50) -> int:
    # PCA9685: 12-bit (0..4095). Period at 50 Hz is 20,000 us.
    period_us = 1_000_000 / freq
    duty = int((us / period_us) * 4096)
    return max(0, min(4095, duty))

def deg_to_us(deg: float) -> float:
    # Map 0..SERVO_RANGE_DEG → SERVO_MIN_US..SERVO_MAX_US
    d = max(0.0, min(SERVO_RANGE_DEG, deg))
    return SERVO_MIN_US + (SERVO_MAX_US - SERVO_MIN_US) * (d / SERVO_RANGE_DEG)

def servo_write(channel: int, deg: float):
    if not USE_PCA9685:
        return
    pulse_us = deg_to_us(deg)
    pca.channels[channel].duty_cycle = us_to_12bit_duty(pulse_us, pca.frequency)

# --- Simple kinematics / mapping -------------------------------
# Store current pos for reporting
current_az = 0.0
current_el = 0.0

# If your azimuth can do 0–360° continuously, you may want to choose shortest-path moves or absolute gearing.
# For hobby pan base, often 0–180° only; clamp and/or gear accordingly.
AZ_OUTPUT_MIN, AZ_OUTPUT_MAX = 0.0, 180.0  # servo limits
EL_OUTPUT_MIN, EL_OUTPUT_MAX = 0.0, 180.0

def map_az_el_to_outputs(az_deg: float, el_deg: float) -> Tuple[float,float]:
    # Clamp logical ranges
    az = max(AZ_MIN_DEG, min(AZ_MAX_DEG, az_deg))
    el = max(EL_MIN_DEG, min(EL_MAX_DEG, el_deg))
    # If your hardware only swings 0–180, compress az into 0–180 (use gearing or accept limited coverage)
    az_out = (az % 360.0) / 360.0 * (AZ_OUTPUT_MAX - AZ_OUTPUT_MIN) + AZ_OUTPUT_MIN
    el_out = (el - EL_MIN_DEG) / (EL_MAX_DEG - EL_MIN_DEG) * (EL_OUTPUT_MAX - EL_OUTPUT_MIN) + EL_OUTPUT_MIN
    return az_out, el_out

# Optional: simple rate limit to avoid snapping the servos
MAX_DEG_PER_STEP = 5.0

def slew_to(az_target: float, el_target: float):
    global current_az, current_el
    az_out, el_out = map_az_el_to_outputs(az_target, el_target)

    # Step in small increments
    steps = max(
        1,
        int(max(abs(az_out - current_az), abs(el_out - current_el)) / MAX_DEG_PER_STEP)
    )
    for i in range(1, steps + 1):
        iaz = current_az + (az_out - current_az) * i / steps
        iel = current_el + (el_out - current_el) * i / steps
        servo_write(AZ_CH, iaz)
        servo_write(EL_CH, iel)
        time.sleep(0.02)  # 50 Hz-ish update

    current_az, current_el = az_out, el_out

# --- Tiny rotctld-like server ----------------------------------
HELP = b"rot_i2c_bridge: commands: p (get), P az el (set), S (stop), q (quit)\n"

async def handle_client(reader: asyncio.StreamReader, writer: asyncio.StreamWriter):
    addr = writer.get_extra_info('peername')
    writer.write(HELP)
    await writer.drain()
    while True:
        data = await reader.readline()
        if not data:
            break
        line = data.decode(errors='ignore').strip()
        if not line:
            continue
        cmd = line.split()
        c0 = cmd[0].lower()

        if c0 == 'p' and len(cmd) == 1:
            # get position
            # Return the Hamlib style two-line response:
            writer.write(f"Azimuth: {current_az:.1f}\n".encode())
            writer.write(f"Elevation: {current_el:.1f}\n".encode())
            await writer.drain()

        elif c0 == 'p' and len(cmd) == 3:
            # Some clients send 'P az el' uppercase; accept lowercase too
            try:
                az = float(cmd[1]); el = float(cmd[2])
                slew_to(az, el)
                writer.write(b"RPRT 0\n")
                await writer.drain()
            except:
                writer.write(b"RPRT -1\n")
                await writer.drain()

        elif c0 == 'P' and len(cmd) == 3:
            # uppercase variant
            try:
                az = float(cmd[1]); el = float(cmd[2])
                slew_to(az, el)
                writer.write(b"RPRT 0\n")
                await writer.drain()
            except:
                writer.write(b"RPRT -1\n")
                await writer.drain()

        elif c0 == 's':
            # stop: implement if you have motion you can abort
            writer.write(b"RPRT 0\n")
            await writer.drain()

        elif c0 in ('q', 'quit', 'exit'):
            break

        elif c0 in ('help', '?'):
            writer.write(HELP)
            await writer.drain()

        else:
            # Unknown; be polite but terse
            writer.write(b"RPRT -8\n")  # command not supported
            await writer.drain()

    writer.close()
    await writer.wait_closed()

async def main():
    server = await asyncio.start_server(handle_client, host='0.0.0.0', port=4533)
    addrs = ", ".join(str(s.getsockname()) for s in server.sockets)
    print(f"Listening on {addrs} (rotctl net)")
    async with server:
        await server.serve_forever()

if __name__ == "__main__":
    asyncio.run(main())

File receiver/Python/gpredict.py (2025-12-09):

#!/usr/bin/env python3
import asyncio
import struct
import time
import board
import busio

# --- Configuration -----------------------
ARDUINO_I2C_ADDR = 0x08  # Must match the Arduino sketch
I2C_BUS_FREQ = 100000    # 100 kHz

# Initialize I2C
i2c = busio.I2C(board.SCL, board.SDA, frequency=I2C_BUS_FREQ)

# Store current pos for reporting (Gpredict expects feedback)
current_az = 0.0
current_el = 0.0


def send_to_arduino(az: float, el: float):
    """
    Packs two floats (little-endian) and writes them to the Arduino.
    Protocol: [AZ_FLOAT][EL_FLOAT] (8 bytes total)
    """
    try:
        # locking is required for CircuitPython busio
        while not i2c.try_lock():
            time.sleep(0.001)  # avoid a tight spin

        # 'f' is a 4-byte float. '<' denotes little-endian (standard for Arduino AVR/ARM)
        payload = struct.pack('<ff', az, el)
        i2c.writeto(ARDUINO_I2C_ADDR, payload)

    except OSError as e:
        print(f"I2C Write Error: {e}")
    finally:
        try:
            i2c.unlock()
        except RuntimeError:
            pass


# --- Rotctld Server ----------------------------------
async def handle_client(reader: asyncio.StreamReader, writer: asyncio.StreamWriter):
    global current_az, current_el

    addr = writer.get_extra_info('peername')
    print(f"Client connected from {addr}")
    
    # --- CRITICAL FIX: REMOVED WELCOME MESSAGE ---
    # Gpredict does not expect a banner. It expects silence until it asks a question.
    # writer.write(b"rot_i2c_bridge ready\n") 
    # await writer.drain()
    # ---------------------------------------------

    while True:
        data = await reader.readline()
        if not data:
            break

        line = data.decode(errors='ignore').strip()
        if not line:
            continue

        print(f"RX: {line!r}")
        cmd = line.split()
        if not cmd:
            continue

        c0 = cmd[0].upper()

        # SET POSITION: P <Az> <El>
        if c0 == 'P' and len(cmd) == 3:
            try:
                target_az = float(cmd[1])
                target_el = float(cmd[2])

                # Update global state
                current_az, current_el = target_az, target_el

                # Send to Arduino immediately
                send_to_arduino(current_az, current_el)

                writer.write(b"RPRT 0\n")
            except ValueError:
                writer.write(b"RPRT -1\n")
            await writer.drain()

        # GET POSITION: p
        elif c0 == 'P' and len(cmd) == 1:
            # Gpredict asks where we are.
            # Sends strictly "AZ\nEL\n"
            response = f"{current_az:.1f}\n{current_el:.1f}\n"
            writer.write(response.encode())
            await writer.drain()

        # STOP: S
        elif c0 == 'S':
            print("Stop command received.")
            writer.write(b"RPRT 0\n")
            await writer.drain()

        # QUIT: q
        elif c0 == 'Q':
            break

        else:
            # Unknown or malformed command
            writer.write(b"RPRT -1\n")
            await writer.drain()

    print(f"Client disconnected from {addr}")
    writer.close()
    await writer.wait_closed()


async def main():
    server = await asyncio.start_server(handle_client, '0.0.0.0', 4533)
    print("Serving rotctld on 0.0.0.0:4533...")
    async with server:
        await server.serve_forever()


if __name__ == "__main__":
    try:
        asyncio.run(main())
    except KeyboardInterrupt:
        print("\nBridge stopped.")

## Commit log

2025-08-25 Add install script for Raspberry Pi SDR stack.
2025-09-10 Modified README for project parameters. Added folder structure.
    [MATS_Power_Subsystem.kicad_sch]
2025-09-12 Added python as as i2c bridge for testing. Included script to help enable I2C and install required libraries.
2025-09-13 Began CAD work for mechanical assembly.
    [Dual-axis servo.SLDPRT, Dual-axis servo.STEP, Single axis servo.STEP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]
2025-09-19 Added Receiver Electrical Schematic Project.
    [Reciever_Electrical.kicad_pcb, Reciever_Electrical.kicad_sch]
2025-09-19 Updated wiring Schematic for Reciever. Added test python scripts.
    [Reciever_Electrical.kicad_sch]
2025-09-22 KiCAD files for the power subsystem
    [Demo-L1.kicad_pcb, Demo-L1.kicad_sch, MATS_Power_Subsystem.kicad_pcb]
2025-09-26 Updated power delivery section of verification test document.
2025-09-27 Added system diagram, subsystem diagram, and test setup/reference material for receiver subsystem.
2025-09-27 Created block diagram for user interface. Added wiring schematic to user interface.
2025-10-03 Added mechanical parts foir rotator.
    [华馨京 25-50kg单轴舵机垫块尺寸图.dwg, 华馨京 25-50kg舵机系列U型机身支架（标准）尺寸图.dwg, 华馨京 25-50kg舵机系列U型舵盘支架（37mm）-3D.STEP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]
2025-10-05 Added print file for rotator assembly.
    [Servo Motor Mount Print.3mf]
2025-11-04 Created mechanical frame components for MATS.
    [001_t_slot_ty3_asm_27.sldasm, 815gf5_2.sldprt, Frame.SLDDRW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]
2025-12-04 Commit for mechanical layout.
    [Base.SLDPRT, Base.stl, Upper_ring_support_x8.SLDPRT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]
